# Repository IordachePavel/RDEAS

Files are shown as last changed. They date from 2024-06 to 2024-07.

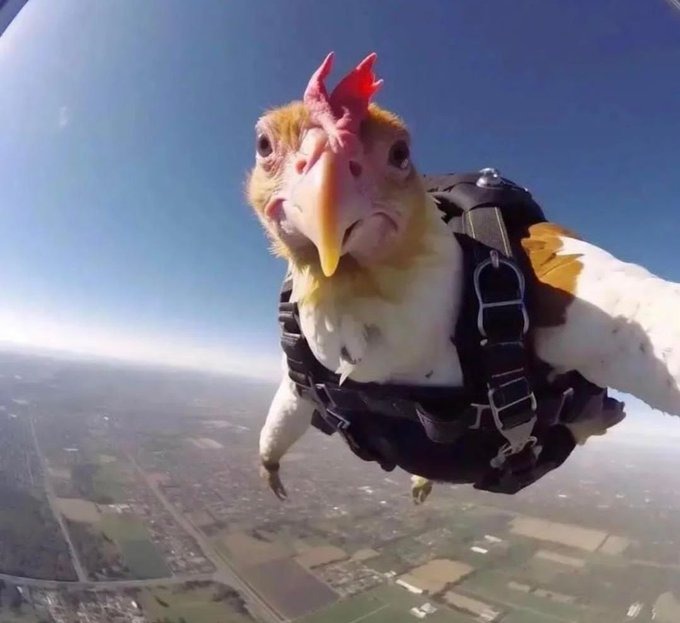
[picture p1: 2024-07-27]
Robot_Controll_doohickey/Resources/skydiving kok [World's funniest image].jpeg

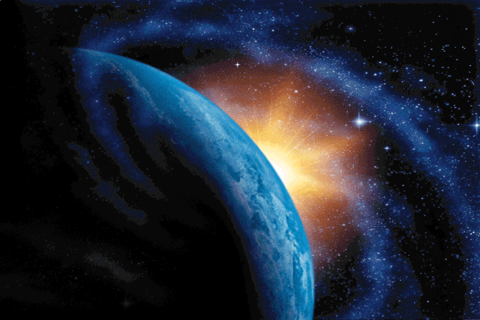
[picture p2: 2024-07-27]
Robot_Controll_doohickey/Resources/background1.bmp

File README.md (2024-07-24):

# Descriere
Remote Dangerous Environment Assessment System (Sistem de Evaluare a Mediilor Periculoase la Distanță)
Sistemul RDEAS este destinat explorării și supravegherii mediilor inaccesibile sau periculoase pentru oameni. Setul RDEAS este compus dintr-un dispozitiv de control la distanță pentru navigație de bază și măsurarea senzorilor, Un set de 2 senzori interschimbabili (Contor Geiger și Senzor de umititate, temperatură și prezența gazelor explozibile), precum și robotul de supraveghere.

# Tehnologii
Sisteme mecanice:
Sistemul este împărțit în 2 părți:

Turela de scanare
Sistem de deplasare

Turela de scanare:


Alcătuită din două motoare , comutatoare de limită și banca de senzori, aceasta se poate roti cu 300° pe orizontală iar banca de senzori cu 270° balans vertical. 

Sistem de deplasare:
Compus din 4 motoare, controlate câte 2 deodată pentru mișcare și viraj tip tanc.

# Sisteme Electronice:
Partea electronică este compusă din:

# Dispozitivul de control
Circuitul de navigare al robotului



Circuitul de interfață pentru senzori

Calculatorul de placă unică „Raspberry Pi 5”


Dispozitivul de control:

Acesta se bazează pe un procesor xscale pocket pc, cu o frecvență de 400MHz, 64 MB de RAM și 64 de ROM, cu o interfață intermediară bazată pe MCU-ul atmel care permite depanarea ușoară și utilizarea unui afișaj de informații secundar. Portul serial DB-9 de pe dispozitiv este conform standardelor RS-232 și poate comunica cu majoritatea dispozitivelor care au o astfel de conexiune. Dispozitivul de control la distanță este echipat cu două baterii, una principală și una secundară. Pentru funcționare, este necesară doar prima. Dispozitivul de control la distanță beneficiază de aproximativ 12 ore de funcționare continuă din prima baterie, iar cea de-a doua baterie este opțională și este utilizată doar pentru a rula pocket pc-ul.

Circuitul de navigare al robotului: Acesta are rolul de control al sistemelor mecanice Pentru calibrarea poziției de 0 a comenzilor de rotire pentru turelă, se folosesc doi senzori magnetici. Banca de senzori este alcătuită dintr-un senzor ultrasonic de distanță, o cameră web și o termopilă digitală IR.

Circuitul de interfață pentru senzori:
Acesta are la bază chipul RP-2040, se ocupă prin interfațarea senzorului interschimbabil și a senzorilor de pe turelă. Acesta preia informațiile de la senzori și îi transmite prin USB la calculatorul de placă unică.
Module de senzori:
Numărător cu tub Geiger-Muller
Senzor temperatură și umiditate ambientală + Senzor concentrație gaz explozibil


Calculatorul de placă unică „Raspberry Pi 5”:
Acesta se ocupă cu procesarea datelor și interpretarea acestora pentru operații autonome, totodată controlând sistemele mecanice și recepționând/transmițând informații de la/la telecomandă prin portul serial, sau prin Ethernet de la/la un calculator.

# Componenta Software:
Componentele software sunt împărțite pe 3 categorii: 1. Program telecomandă 2. Programul microcontroller robot Program telecomandă: Scris in C# pentru platforma Windows Mobile, utilizând sistemele .NET Compact pentru interfața grafică și alte funcții „Low-level”, este folosit pentru interacționarea dintre utilizator și robot. Aceasta are 2 funcții principale.

Terminal serial RS-232
Telecomandă robot Primul mod reprezintă o interfață pentru orice sistem cu o conecțiune serial RS-232, unde utilizatorul poate trimite și recepționa mesaje la/de la dispozitivul conectat, sau pentru depanarea robotului. Al doilea mod reprezintă o telecomandă simplificată a robotului, unde utilizatorul poate controla funcțiile robotului prin intermediul butoanelor de pe ecran.

Programele microcontrolerelor robotului: Aceasta are ca scop traducerea comenziilor de la telecomandă în semnale de acționare a motoarelor, interpretarea și transmiterea semnalelor de la senzori.

Programe pe SBC-ul Raspberry Pi 5 : Acestea se ocupă cu recepționarea comenzilor, interpretarea acestora, codificarea/decodificarea de date pentru transmitere, controlul sistemelor mecanice, interfață electronice senzori și afișaj cameră.

# Cerinte sistem
Operare de bază (Fără cameră, mod teleghidat): 
Doar telecomanda și robotul, cablu serial, Mufă DB-9, distanța maximă variază cu rata de baud.
Operare avansată:
Hardware: Laptop/Computer cu port Ethernet, Cablu Cat5 cu mufă Ethernet.
Software: Windows 7/8/8.1/10/11, Microsoft .NET (Latest)

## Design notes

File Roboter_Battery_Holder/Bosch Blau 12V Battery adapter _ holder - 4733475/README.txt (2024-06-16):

Bosch Blau 12V Battery adapter / holder by Knrd on Thingiverse: https://www.thingiverse.com/thing:4733475

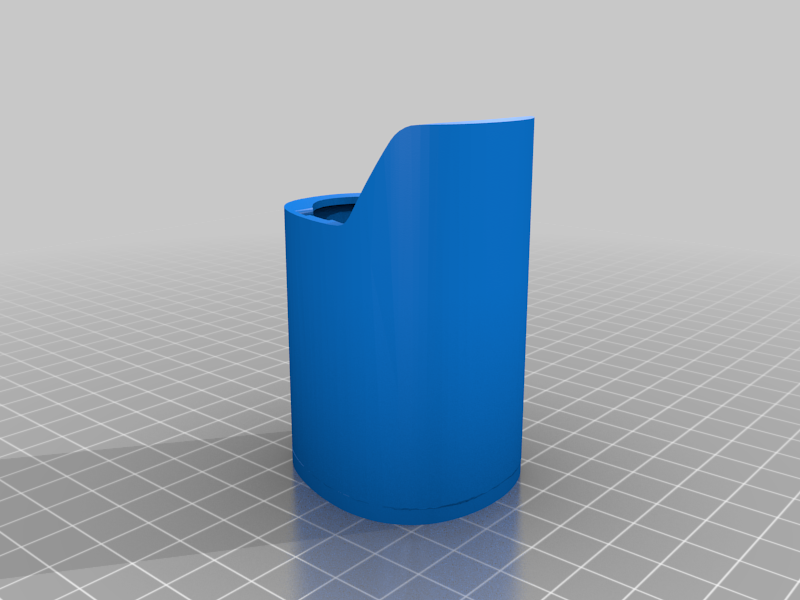
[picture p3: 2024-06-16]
Roboter_Battery_Holder/Bosch Blau 12V Battery adapter _ holder - 4733475/images/Bosch_12V_Battery_Holder.png

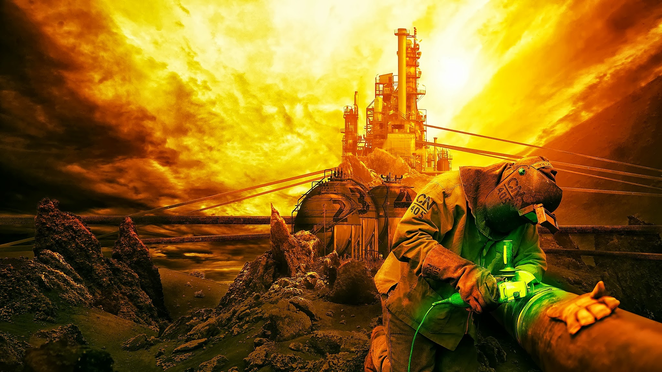
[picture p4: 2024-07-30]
Robot_Controll_doohickey/Resources/factorio man foarte tare.png

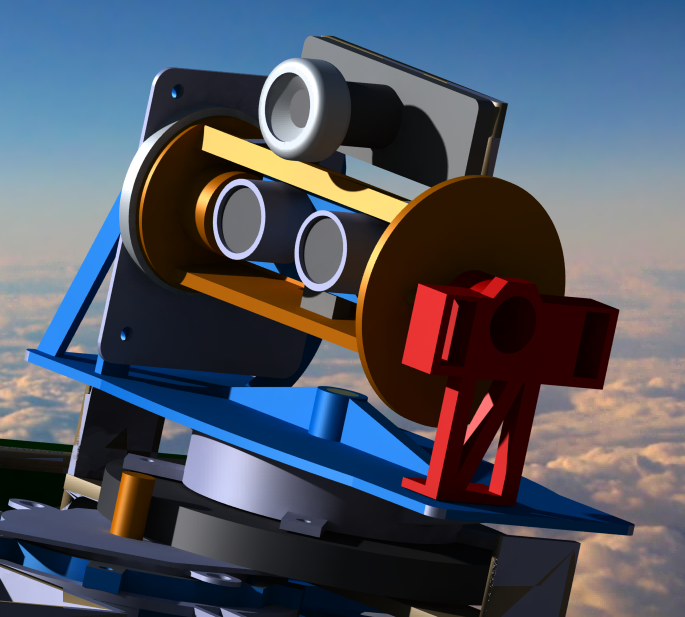
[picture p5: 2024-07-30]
Robot_Controll_doohickey/Resources/SensorTurret.png

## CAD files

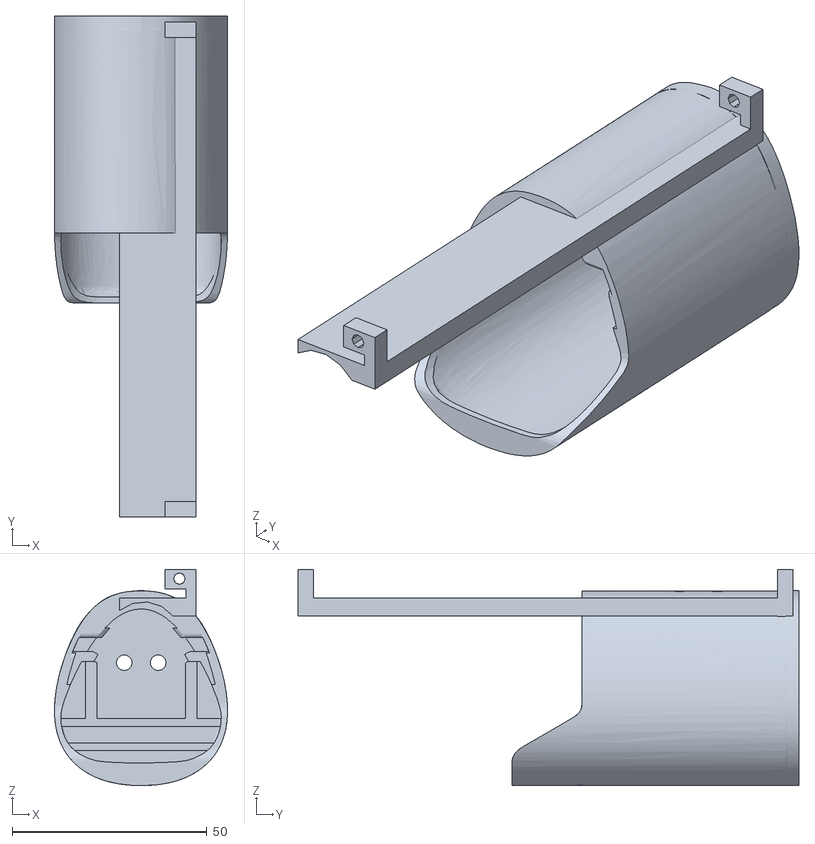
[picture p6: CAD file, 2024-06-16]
Roboter_Battery_Holder/Batery_mount.stl
44.4 x 128.5 x 55.5

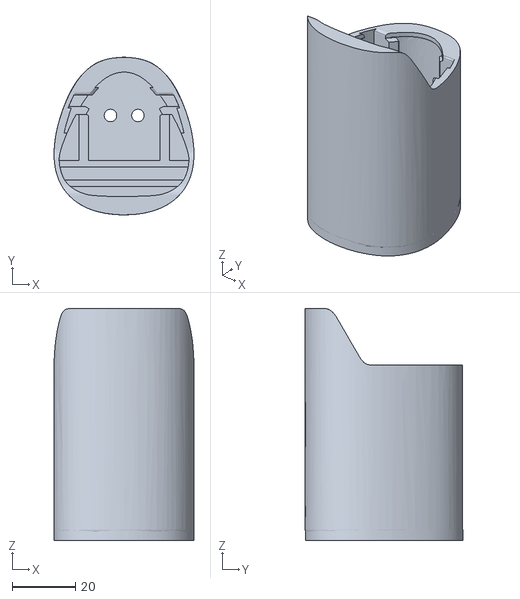
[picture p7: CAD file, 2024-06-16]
Roboter_Battery_Holder/Bosch Blau 12V Battery adapter _ holder - 4733475/files/Bosch_12V_Battery_Holder.stl
44.4 x 50.1 x 73.6

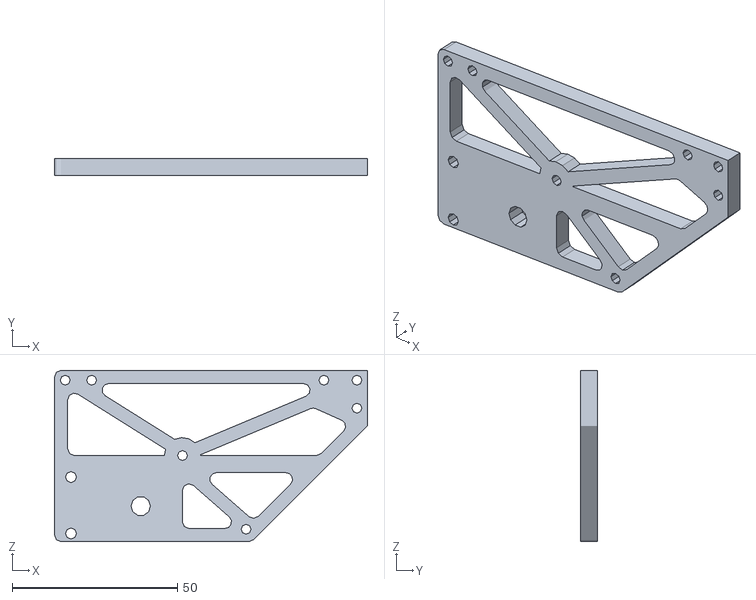
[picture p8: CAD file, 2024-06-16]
Roboter_Chassis/Revision I/Lateral_MotorMount_Frame.stl
94.8 x 5.00 x 51.9

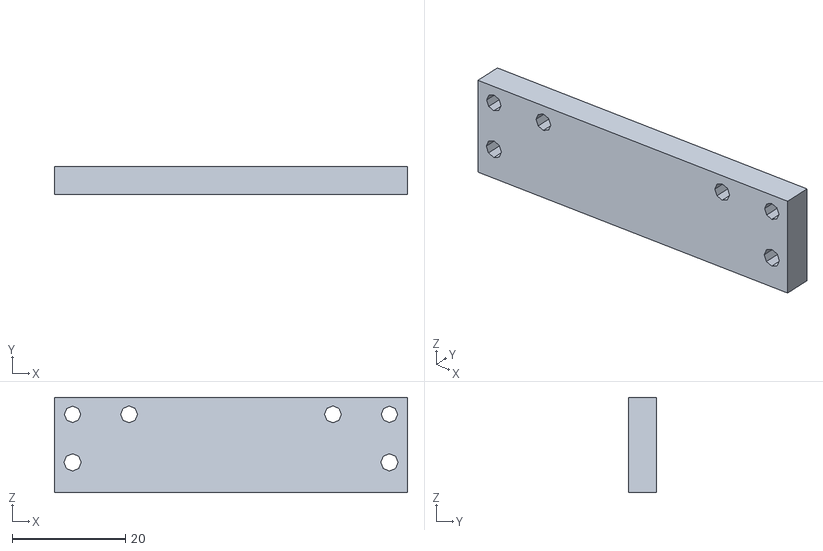
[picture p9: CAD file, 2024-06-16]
Roboter_Chassis/Revision I/Lateral_MotorMount_Frame_JoinArm.stl
62.5 x 5.00 x 16.8

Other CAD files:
AtmosSensorModuleCase/GeigerSensorCase.CATPart
AtmosSensorModuleCase/ModuleSensCap.CATProduct
PDA_REMOTE_CASE/Backside.CATPart
PDA_REMOTE_CASE/Battery Holders.CATPart
PDA_REMOTE_CASE/Casing 1 Rev 2.CATPart
PDA_REMOTE_CASE/Casing 1,.CATPart
PDA_REMOTE_CASE/Casing B.CATPart
PDA_REMOTE_CASE/Casing, 1, side 1.CATPart
PDA_REMOTE_CASE/Casing.CATPart
PDA_REMOTE_CASE/Component_front_panel_1.CATPart
PDA_REMOTE_CASE/Electronics Demo Stand 2.CATPart
PDA_REMOTE_CASE/Electronics Demo Stand.CATPart
PDA_REMOTE_CASE/I don't kow.CATPart
PDA_REMOTE_CASE/IR_THERMOPILE_SENSOR.CATProduct
PDA_REMOTE_CASE/Interface PDA & interpereter display.CATPart
PDA_REMOTE_CASE/Microwave.CATProduct
PDA_REMOTE_CASE/Mini USB B Port.CATPart
PDA_REMOTE_CASE/PDA.CATPart
PDA_REMOTE_CASE/PDA.CATProduct
PDA_REMOTE_CASE/Part1.CATPart
PDA_REMOTE_CASE/Pda-Midframe.CATPart
PDA_REMOTE_CASE/Pushbutton.CATPart
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

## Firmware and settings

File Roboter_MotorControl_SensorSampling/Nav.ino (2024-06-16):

// THIS IS NAVIGATION CIRCUIT CONTROLLER PROGRAM.

//Needed for I2C THERMOPILE SENSOR
#include <Wire.h>

//SENSOR DEFINITIONS
const int trigPin = 16;  //Ultrasonic sensor
const int echoPin = 10; 


#define D6T_ADDR 0x0A  // for I2C 7bit address
#define D6T_CMD 0x4C 

#define PARA_0100MS_1	((uint8_t)0x90)
#define PARA_0100MS_2	((uint8_t)0xDA)
#define PARA_0100MS_3	((uint8_t)0x16)

#define N_ROW 1
#define N_PIXEL 1
#define N_READ ((N_PIXEL + 1) * 2 + 1)

uint8_t rbuf[N_READ];
int16_t pix_data = 0;
int16_t seqData[40] = {0};

float duration, distance; 
uint16_t  totalCount = 0;

//TERMOPILE SENSOR SETTINGS (1)
#define comparingNumInc 16 // x samplingTime ms   (range: 1 to 39)  (example) 16 x 100 ms -> 1.6 sec
#define comparingNumDec 16  // x samplingTime ms  (range: 1 to 39)  (example) 16 x 100 ms -> 1.6 sec
#define threshHoldInc 10 //  /10 degC   (example) 10 -> 1.0 degC (temperature change > 1.0 degC -> Enable)  
#define threshHoldDec 10 //  /10 degC   (example) 10 -> 1.0 degC (temperature change > 1.0 degC -> Disable)

//TERMOPILE SENSOR SETTINGS (2)
#define samplingTime 100

// CONTROL MESSAGE VARIABLE
String MSG;

// SCANNING HEAD CONTROL PINS
const short unsigned int SW_Rot_Lim_1=8;//Rotation Limit Switch Right
const short unsigned int SW_Rot_Lim_2=7;//Rotation Limit Switch Left
const short unsigned int SW_Pit_Lim_1=6;//Pitch Limit Switch Closer
const short unsigned int SW_Pit_Lim_2=9;//Pitch Limit Switch Further
const short unsigned int DriverPitch_Dir=A3;//(Analog pin 3)Pitch motor driver direction
const short unsigned int DriverPitch_Step=A2;//(Analog pin 2)Pitch motor driver step command
const short unsigned int DriverRotation_Dir=4;//Rotation motor driver direction
const short unsigned int DriverRotation_Step=5;//Rotation motor driver step command

const int ButtonCheckCount =100;//How many times to check the switches if they've been triggered during the homing process

// MOVEMENT CONTROL PINS

const short unsigned int T_bridge_Left_Forward = A1;
const short unsigned int T_bridge_Left_Backwards = A0;
const short unsigned int T_bridge_Right_Forward = 15;
const short unsigned int T_bridge_Right_Backwards = 14;   

// MOVEMENT CONTROL VARIABLES
int moveCounter=0;
char dir='F';
// PITCH CONTROL
bool pitchA = false;
bool pitchB = false;
bool yawA = false;
bool yawB = false;


/** <!-- D6T_checkPEC {{{ 1--> D6T PEC(Packet Error Check) calculation.
 * calculate the data sequence,
 * from an I2C Read client address (8bit) to thermal data end.
 */
uint8_t calc_crc(uint8_t data) {
    int index;
    uint8_t temp;
    for (index = 0; index < 8; index++) {
        temp = data;
        data <<= 1;
        if (temp & 0x80) {data ^= 0x07;}
    }
    return data;
}

bool D6T_checkPEC(uint8_t buf[], int n) {
    int i;
    uint8_t crc = calc_crc((D6T_ADDR << 1) | 1);  // I2C Read address (8bit)
    for (i = 0; i < n; i++) {
        crc = calc_crc(buf[i] ^ crc);
    }
    bool ret = crc != buf[n];
    if (ret) {
        Serial.print("PEC check failed:");
        Serial.print(crc, HEX);
        Serial.print("(cal) vs ");
        Serial.print(buf[n], HEX);
        Serial.println("(get)");
    }
    return ret;
}
//PEC END

/** <!-- conv8us_s16_le {{{1 --> convert a 16bit data from the byte stream.
 */
int16_t conv8us_s16_le(uint8_t* buf, int n) {
    int ret;
    ret = buf[n];
    ret += buf[n + 1] << 8;
    return (int16_t)ret;   // and convert negative.
}


// Compare two strings
bool cmpNstr(String a, String b,int n){
  for(int i=0;i<n;i++){
    if(a[i]!=b[i])
    return 0;
  }
  return 1;
}
// Convert message on Serial to task
void MessageInterpreter(char comm){
  int opVal=comm-48;
  if(opVal>0){
    delay(500);
  Serial1.print("RCV");
  Serial.print("Message Awknowledged: ");
  Serial.print(comm);
  }
  switch(opVal){
    case 1:
    Serial1.println("RX OK!");
    break;
    case 2:
    break;
    case 3:
    break;
    case ('F'-48):
    dir='F';
    moveCounter=MSG.substring(5).toInt();
    Serial.println(moveCounter);
    break;
    case ('B'-48):
    dir='B';
    moveCounter=MSG.substring(5).toInt();
    Serial.println(moveCounter);
    break;
    case ('R'-48):
    dir='R';
    moveCounter=MSG.substring(5).toInt();
    Serial.println(moveCounter);
    break;
    case ('L'-48):
    dir='L';
    moveCounter=MSG.substring(5).toInt();
    Serial.println(moveCounter);
    break;
    case ('U'-48):
    digitalWrite(DriverPitch_Dir, 1);
    dir='U'; 
    moveCounter=MSG.substring(5).toInt();
    break;
    case ('D'-48):
    digitalWrite(DriverPitch_Dir, 0);
    dir='D';
    moveCounter=MSG.substring(5).toInt();
    break;
    case ('X'-48):
    digitalWrite(DriverRotation_Dir, 1);
    dir='X';
    moveCounter=MSG.substring(5).toInt();
    break;
    case ('Y'-48):
    digitalWrite(DriverRotation_Dir, 0);
    dir='Y';
    moveCounter=MSG.substring(5).toInt();
    break;
    case ('N'-48):
    moveCounter=1;
    break;
    case ('T'-48):
    TempTarget(0);
    break;
    case('S'-48):
    TempTarget(1);
    break;
    case('P'-48):
    DistTarget();
    break;
  }
  opVal=0;
}

bool HomeYawMotor(){
  yawA = false;
  yawB = false;
  bool SwitchAState = !digitalRead(SW_Rot_Lim_1);
  bool SwitchBState = !digitalRead(SW_Rot_Lim_2);
  if(SwitchAState && SwitchBState){
    return true;
  }
  digitalWrite(DriverRotation_Dir, 1);
  for (int i=0;i<380 && !(yawA && yawB);i++){
    digitalWrite(DriverRotation_Step,HIGH);
    delayMicroseconds(2000);
    digitalWrite(DriverRotation_Step,LOW);
    delayMicroseconds(2000);
    if(SwitchAState != !digitalRead(SW_Rot_Lim_1)){
      yawA = true;
    }
    if(SwitchBState != !digitalRead(SW_Rot_Lim_2)){
      yawB = true;
    }
  }
  digitalWrite(DriverRotation_Dir, 0);
  for (int i=0;i<380*2 && !(yawA && yawB);i++){
    digitalWrite(DriverRotation_Step,HIGH);
    delayMicroseconds(2000);
    digitalWrite(DriverRotation_Step,LOW);
    delayMicroseconds(2000);
    if(SwitchAState != !digitalRead(SW_Rot_Lim_1)){
      yawA = true;
    }
    if(SwitchBState != !digitalRead(SW_Rot_Lim_2)){
      yawB = true;
    }
  }
  if(yawA&&yawB){ // Go just three more steps due to how the magnetic field is aligned to the sensor, it triggers earlier
    for(int i=0;i<3;i++){
    digitalWrite(DriverRotation_Step,HIGH);
    delayMicroseconds(2000);
    digitalWrite(DriverRotation_Step,LOW);
    delayMicroseconds(2000);
    }
  }
    return(yawA&&yawB);
}

bool HomePitchMotor(){
  pitchA = false;
  pitchB = false;
  bool SwitchAState = !digitalRead(SW_Pit_Lim_1);
  bool SwitchBState = !digitalRead(SW_Pit_Lim_2);
  if(SwitchAState && SwitchBState){
    return true;
  }
  digitalWrite(DriverPitch_Dir, 1);
  for (int i=0;i<246 && !(pitchA && pitchB);i++){
    digitalWrite(DriverPitch_Step,HIGH);
    delayMicroseconds(2000);
    digitalWrite(DriverPitch_Step,LOW);
    delayMicroseconds(2000);
    if(SwitchAState != !digitalRead(SW_Pit_Lim_1)){
      pitchA = true;
    }
    if(SwitchBState != !digitalRead(SW_Pit_Lim_2)){
      pitchB = true;
    }
  }
  digitalWrite(DriverPitch_Dir, 0);
  for (int i=0;i<256*2 && !(pitchA && pitchB);i++){
    digitalWrite(DriverPitch_Step,HIGH);
    delayMicroseconds(2000);
    digitalWrite(DriverPitch_Step,LOW);
    delayMicroseconds(2000);
    if(SwitchAState != !digitalRead(SW_Pit_Lim_1)){
      pitchA = true;
    }
    if(SwitchBState != !digitalRead(SW_Pit_Lim_2)){
      pitchB = true;
    }
  }
  if(pitchA&&pitchB){ // Go just three more steps due to how the magnetic field is aligned to the sensor, it triggers
    for(int i=0;i<3;i++){
    digitalWrite(DriverPitch_Step,HIGH);
    delayMicroseconds(2000);
    digitalWrite(DriverPitch_Step,LOW);
    delayMicroseconds(2000);
    }
  }
    return(pitchA&&pitchB);
}

void TempTarget (bool RQST){
    int i, j;

    memset(rbuf, 0, N_READ);
    // Wire buffers are enough to read D6T-16L data (33bytes) with
    // MKR-WiFi1010 and Feather ESP32,
    // these have 256 and 128 buffers in their libraries.
    Wire.beginTransmission(D6T_ADDR);  // I2C client address
    Wire.write(D6T_CMD);               // D6T register
    Wire.endTransmission();            // I2C repeated start for read
    Wire.requestFrom(D6T_ADDR, N_READ);
    i = 0;
    while (Wire.available()) {
        rbuf[i++] = Wire.read();
    }

    if (D6T_checkPEC(rbuf, N_READ - 1)) {
        return;
    }

    // 1st data is PTAT measurement (: Proportional To Absolute Temperature)
    int16_t itemp = conv8us_s16_le(rbuf, 0);
    if(RQST){
    Serial1.print(itemp / 10.0, 1);
    }

    // loop temperature pixels of each thrmopiles measurements
    for (i = 0, j = 2; i < N_PIXEL; i++, j += 2) {
        itemp = conv8us_s16_le(rbuf, j);
        pix_data = itemp;
        if(!RQST){
          Serial1.print("TMP");
          Serial1.print(itemp / 10.0, 1);  // print PTAT & Temperature
            Serial1.print('\n');   // print delimiter
        }
        }
    }

void DistTarget (){
  digitalWrite(trigPin, LOW);
  delayMicroseconds(2);
  digitalWrite(trigPin, HIGH);
  delayMicroseconds(10);
  digitalWrite(trigPin, LOW);

  duration = pulseIn(echoPin, HIGH);
  distance = (duration*.0343)/2;
  distance = round(distance*100);
  Serial1.print("DST");
  Serial1.print((int)distance);
}

void setup() {
  //Pindef ultrasonics
  pinMode(trigPin, OUTPUT);  
	pinMode(echoPin, INPUT); 
  //Serial1 I/O (UART)
  Serial1.begin(9600);
  //Serial I/O (USB, Debug)
  Serial.begin(9600);

  //Sensor Init Config Block START
  uint8_t para[3] = {0};
    para[0] = PARA_0100MS_1;
		para[1] = PARA_0100MS_2;
		para[2] = PARA_0100MS_3;
 
 
    Serial.begin(115200);  // Serial baudrate = 115200bps
    Wire.begin();  // i2c master

    Wire.beginTransmission(D6T_ADDR);  // I2C client address
    Wire.write(0x02);                  // D6T register
    Wire.write(0x00);                  // D6T register
    Wire.write(0x01);                  // D6T register
    Wire.write(0xEE);                  // D6T register
    Wire.endTransmission();            // I2C repeated start for read
    Wire.beginTransmission(D6T_ADDR);  // I2C client address
    Wire.write(0x05);                  // D6T register
    Wire.write(para[0]);                  // D6T register
    Wire.write(para[1]);                  // D6T register
    Wire.write(para[2]);                  // D6T register
    Wire.endTransmission();            // I2C repeated start for read
    Wire.beginTransmission(D6T_ADDR);  // I2C client address
    Wire.write(0x03);                  // D6T register
    Wire.write(0x00);                  // D6T register
    Wire.write(0x03);                  // D6T register
    Wire.write(0x8B);                  // D6T register
    Wire.endTransmission();            // I2C repeated start for read
    Wire.beginTransmission(D6T_ADDR);  // I2C client address
    Wire.write(0x03);                  // D6T register
    Wire.write(0x00);                  // D6T register
    Wire.write(0x07);                  // D6T register
    Wire.write(0x97);                  // D6T register
    Wire.endTransmission();            // I2C repeated start for read
    Wire.beginTransmission(D6T_ADDR);  // I2C client address
    Wire.write(0x02);                  // D6T register
    Wire.write(0x00);                  // D6T register
    Wire.write(0x00);                  // D6T register
    Wire.write(0xE9);                  // D6T register
    Wire.endTransmission();            // I2C repeated start for read	
  //Sensor Init Config Block END
  

  //Limit switches
  pinMode(SW_Rot_Lim_1,INPUT_PULLUP);
  pinMode(SW_Rot_Lim_2,INPUT_PULLUP);
  pinMode(SW_Pit_Lim_1,INPUT_PULLUP);
  pinMode(SW_Pit_Lim_2,INPUT_PULLUP);
  //Head control
  pinMode(DriverPitch_Dir,OUTPUT);
  digitalWrite(DriverPitch_Dir,LOW);
  pinMode(DriverPitch_Step,OUTPUT);
  digitalWrite(DriverPitch_Step,LOW);
  pinMode(DriverRotation_Dir,OUTPUT);
  digitalWrite(DriverRotation_Dir,LOW);
  pinMode(DriverRotation_Step,OUTPUT);
  digitalWrite(DriverRotation_Step,LOW);
  //Movement control
  pinMode(T_bridge_Left_Backwards, OUTPUT);
  digitalWrite(T_bridge_Left_Backwards, LOW);
  pinMode(T_bridge_Left_Forward,OUTPUT);
  digitalWrite(T_bridge_Left_Forward,LOW);
  pinMode(T_bridge_Right_Backwards,OUTPUT);
  digitalWrite(T_bridge_Right_Backwards,LOW);
  pinMode(T_bridge_Right_Forward,OUTPUT);
  digitalWrite(T_bridge_Right_Forward,LOW);

  //Homing
  if(!HomeYawMotor()){
    Serial.println("Motor failure! Check machine.");
    for(;;);//You don't want the machine to tangle its wires.
  }
  else{
    Serial.println("Yaw motor homing OK!");
  }
  if(!HomePitchMotor()){
    Serial.println("Motor failure! Check machine.");
    for(;;);//Same here.
  }
  else{
    Serial.println("Pitch motor homing OK!");
  }
  delay(100);
  Serial.println("Motor homing success!");
}

void loop() {
  if(Serial1.available() > 0){
  MSG=Serial1.readString();
  if (cmpNstr(MSG,"NAV",3))
  
  MessageInterpreter(MSG[4]);
  }
  //Movement logic (must be in loop so the MCU can switch between driving the motors, running the counter for the motors and using navigation sensors)
  if(moveCounter){
    switch (dir) {
    case 'F':
    digitalWrite(T_bridge_Left_Backwards,LOW);
    digitalWrite(T_bridge_Right_Backwards,LOW);
    digitalWrite(T_bridge_Left_Forward,HIGH);
    digitalWrite(T_bridge_Right_Forward,HIGH);
    break;
    case 'B':
    digitalWrite(T_bridge_Left_Forward,LOW);
    digitalWrite(T_bridge_Right_Forward,LOW);
    digitalWrite(T_bridge_Left_Backwards,HIGH);
    digitalWrite(T_bridge_Right_Backwards,HIGH);
    break;
    case 'R':
    digitalWrite(T_bridge_Left_Forward,HIGH);
    digitalWrite(T_bridge_Right_Forward,LOW);
    digitalWrite(T_bridge_Left_Backwards,LOW);
    digitalWrite(T_bridge_Right_Backwards,HIGH);
    break;
    case 'L':
    digitalWrite(T_bridge_Left_Forward,LOW);
    digitalWrite(T_bridge_Right_Forward,HIGH);
    digitalWrite(T_bridge_Left_Backwards,HIGH);
    digitalWrite(T_bridge_Right_Backwards,LOW);
    break;
    case 'U':
    digitalWrite(DriverPitch_Step,HIGH);
    delayMicroseconds(2000);
    digitalWrite(DriverPitch_Step,LOW);
    delayMicroseconds(2000);
    break;
    case 'D':
    digitalWrite(DriverPitch_Step,HIGH);
    delayMicroseconds(2000);
    digitalWrite(DriverPitch_Step,LOW);
    delayMicroseconds(2000);
    break;
    case 'X':
    digitalWrite(DriverRotation_Step,HIGH);
    delayMicroseconds(2000);
    digitalWrite(DriverRotation_Step,LOW);
    delayMicroseconds(2000);
    break;
    case 'Y':
    digitalWrite(DriverRotation_Step,HIGH);
    delayMicroseconds(2000);
    digitalWrite(DriverRotation_Step,LOW);
    delayMicroseconds(2000);
    break;
    }
    moveCounter--;
    Serial.println(moveCounter);
    Serial.print(dir);
    if(moveCounter == 1){
      DistTarget();
    }
  }
  else{
    digitalWrite(T_bridge_Left_Backwards,LOW);
    digitalWrite(T_bridge_Left_Forward,LOW);
    digitalWrite(T_bridge_Right_Backwards,LOW);
    digitalWrite(T_bridge_Right_Forward,LOW);
  }

}

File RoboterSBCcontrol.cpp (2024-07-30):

#include <iostream>
#include <unistd.h>
#include <sys/socket.h>
#include <netinet/in.h>
#include <string>
#include <cstring>
#include <wiringPi.h>
#include <libserialport.h>
#include <thread>
#include <sstream>

#define Right_T_bridge_Forwards 12
#define Right_T_bridge_Backwards 13
#define Left_T_bridge_Forwards 14
#define Left_T_bridge_Backwards 21
#define Rot_Stp 2
#define Rot_Dir 3
#define Pit_Stp 22
#define Pit_Dir 23
#define Sw_Rot_Lim_1 7
#define Sw_Rot_Lim_2 9
#define Sw_Pit_Lim_1 8
#define Sw_Pit_Lim_2 0

char PinMotorCommand = 'S';
bool StepperCommandEnable = false;
bool AlreadyStopped = true;
bool AlreadyStoppedRotation = true;

sp_port *port1;
sp_port *port2;
sp_port *raspberryPiUartPort; // New serial port for Raspberry Pi UART

// Function prototypes
void configure_port(sp_port *port);
void initialize_serial_ports();
void close_serial_ports();
void SendUSBUART1(const std::string &message);
void SendUSBUART2(const std::string &message);
std::string ReceiveUSBUART(sp_port *port);
void handleRotCommand(char movCommand);
void StepperMovementHandler(char movCommand);
void handleMovCommand(char movCommand);
void handleSNSCommand(char command);
void interpretMessage(const std::string& message);
void forwardMessageToClient(const std::string &message, int client_socket);
void handleRaspberryPiUartCommunication();

void configure_port(sp_port *port) {
    sp_set_baudrate(port, 9600);
    sp_set_bits(port, 8);
    sp_set_parity(port, SP_PARITY_NONE);
    sp_set_stopbits(port, 1);
    sp_set_flowcontrol(port, SP_FLOWCONTROL_NONE);
}

void initialize_serial_ports() {
    if (sp_get_port_by_name("/dev/ttyACM1", &port2) != SP_OK) {
        std::cerr << "Failed to get port /dev/ttyACM1" << std::endl;
        exit(1);
    }
    if (sp_open(port2, SP_MODE_READ_WRITE) != SP_OK) {
        std::cerr << "Failed to open port /dev/ttyACM1" << std::endl;
        exit(1);
    }
    configure_port(port2);

    if (sp_get_port_by_name("/dev/ttyACM0", &port1) != SP_OK) {
        std::cerr << "Failed to get port /dev/ttyACM0" << std::endl;
        sp_close(port1);
        exit(1);
    }
    if (sp_open(port1, SP_MODE_READ_WRITE) != SP_OK) {
        std::cerr << "Failed to open port /dev/ttyACM0" << std::endl;
        sp_close(port1);
        exit(1);
    }
    configure_port(port1);

    // Open Raspberry Pi UART port
    if (sp_get_port_by_name("/dev/ttyAMA0", &raspberryPiUartPort) != SP_OK) {
        std::cerr << "Failed to get port /dev/ttyAMA0" << std::endl;
        sp_close(port1);
        sp_close(port2);
        exit(1);
    }
    if (sp_open(raspberryPiUartPort, SP_MODE_READ_WRITE) != SP_OK) {
        std::cerr << "Failed to open port /dev/ttyAMA0" << std::endl;
        sp_close(port1);
        sp_close(port2);
        exit(1);
    }
    configure_port(raspberryPiUartPort);
}

void close_serial_ports() {
    sp_close(port1);
    sp_close(port2);
    sp_close(raspberryPiUartPort);
    sp_free_port(port1);
    sp_free_port(port2);
    sp_free_port(raspberryPiUartPort);
}

void SendUSBUART1(const std::string &message) {
    sp_nonblocking_write(port1, message.c_str(), message.length());
}

void SendUSBUART2(const std::string &message) {
    sp_nonblocking_write(port2, message.c_str(), message.length());
}

std::string ReceiveUSBUART(sp_port *port) {
    char buffer[1024];
    int bytes_read = sp_blocking_read(port, buffer, sizeof(buffer) - 1, 1000); // Timeout of 1000 ms
    if (bytes_read > 0) {
        buffer[bytes_read] = '\0';
        return std::string(buffer);
    }
    return "";
}

void handleRotCommand(char movCommand) {
    StepperCommandEnable = true;
    PinMotorCommand = movCommand;
    std::cout << "Handling ROT command: " << movCommand << std::endl;
}

bool HomeYawMotor(){
    std::cout << "Homing yaw" << std::endl;
  bool yawA = false;
  bool yawB = false;
  bool SwitchAState = !digitalRead(Sw_Rot_Lim_1);
  bool SwitchBState = !digitalRead(Sw_Rot_Lim_2);
  if(SwitchAState && SwitchBState){
    return true;
  }
  digitalWrite(Rot_Dir, 1);
  for (int i=0;i<380 && !(yawA && yawB);i++){
    digitalWrite(Rot_Stp,HIGH);
    delay(5);
    digitalWrite(Rot_Stp,LOW);
    delay(5);
    if(SwitchAState != !digitalRead(Sw_Rot_Lim_1)){
      yawA = true;
    }
    if(SwitchBState != !digitalRead(Sw_Rot_Lim_2)){
      yawB = true;
    }
  }
  digitalWrite(Rot_Dir, 0);
  for (int i=0;i<380*2 && !(yawA && yawB);i++){
    digitalWrite(Rot_Stp,HIGH);
    delay(5);
    digitalWrite(Rot_Stp,LOW);
    delay(5);
    if(SwitchAState != !digitalRead(Sw_Rot_Lim_1)){
      yawA = true;
    }
    if(SwitchBState != !digitalRead(Sw_Rot_Lim_2)){
      yawB = true;
    }
  }
  if(yawA&&yawB){ // Go just three more steps due to how the magnetic field is aligned to the sensor, it triggers earlier
    for(int i=0;i<3;i++){
    digitalWrite(Rot_Stp,HIGH);
    delay(5);
    digitalWrite(Rot_Stp,LOW);
    delay(5);
    }
  }
    return(yawA&&yawB);
}

bool HomePitchMotor(){
  bool pitchA = false;
  bool pitchB = false;
  bool SwitchAState = !digitalRead(Sw_Pit_Lim_1);
  bool SwitchBState = !digitalRead(Sw_Pit_Lim_2);
  if(SwitchAState && SwitchBState){
    return true;
  }
  digitalWrite(Pit_Stp, 1);
  for (int i=0;i<246 && !(pitchA && pitchB);i++){
    digitalWrite(Pit_Stp,HIGH);
    delay(2);
    digitalWrite(Pit_Stp,LOW);
    delay(2);
    if(SwitchAState != !digitalRead(Sw_Pit_Lim_1)){
      pitchA = true;
    }
    if(SwitchBState != !digitalRead(Sw_Pit_Lim_2)){
      pitchB = true;
    }
  }
  digitalWrite(Pit_Dir , 0);
  for (int i=0;i<256*2 && !(pitchA && pitchB);i++){
    digitalWrite(Pit_Stp,HIGH);
    delay(2);
    digitalWrite(Pit_Stp,LOW);
    delay(2);
    if(SwitchAState != !digitalRead(Sw_Pit_Lim_1)){
      pitchA = true;
    }
    if(SwitchBState != !digitalRead(Sw_Pit_Lim_2)){
      pitchB = true;
    }
  }
  if(pitchA&&pitchB){ // Go just three more steps due to how the magnetic field is aligned to the sensor, it triggers
    for(int i=0;i<3;i++){
    digitalWrite(Pit_Stp,HIGH);
    delay(2);
    digitalWrite(Pit_Stp,LOW);
    delay(2);
    }
  }
    return(pitchA&&pitchB);
}

void StepperMovementHandler(char movCommand) {
    if (movCommand == 'B') {
        digitalWrite(Rot_Dir, HIGH);
        digitalWrite(Rot_Stp, HIGH);
        delay(2);
        digitalWrite(Rot_Stp, LOW);
        digitalWrite(Rot_Dir, LOW);
    } else if (movCommand == 'D') {
        digitalWrite(Pit_Dir, HIGH);
        digitalWrite(Pit_Stp, HIGH);
        delay(2);
        digitalWrite(Pit_Stp, LOW);
        digitalWrite(Pit_Dir, LOW);
    } else if (movCommand == 'A') {
        digitalWrite(Rot_Stp, HIGH);
        delay(2);
        digitalWrite(Rot_Stp, LOW);
    } else if (movCommand == 'C') {
        digitalWrite(Pit_Stp, HIGH);
        delay(2);
        digitalWrite(Pit_Stp, LOW);
    }
}
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

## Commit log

2024-06-18 Rename HEY LOIS IM MIDFRAME.CATPart to Pda-Midframe.CATPart
    [Pda-Midframe.CATPart]
2024-07-02 Update PDA_MCU_INTERFACE.ino
    The gaming update (Support for joysticks in order to send control via serial, added ability for the PDA to change the baud rate at will, which originally was stuck to 9600 baud.)
    [PDA_MCU_INTERFACE.ino]
2024-07-02 Update PDA_MCU_INTERFACE.ino
    Whoopsies, small display order error, junk text from last message would remain, added clean function where possible.
    [PDA_MCU_INTERFACE.ino]
2024-07-24 Create Sensor_Module_Reader.ino
    Logic for the modular sensor reader
2024-07-24 Create Sensor_AmbientTemperatureHumidity_EGM.ino
    Logic for the ambient temperature, humidity, and explosive gas concentration in the atmosphere sensor.
2024-07-27 Modular sensor cases
    [GeigerSensorCase.CATPart, ModuleSensCap.CATProduct]
2024-07-27 New desktop robot control program 1.0
    New desktop control program that allows the user to control the robot via LAN connection, enabling sensor measurement requests and movement control. This version has PDA remote control in serial joys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
2024-07-27 Create Turret_Sensor_5V_Controller.ino
    Additional MCU to handle talking to the 5V sensor. I ain't taking care of stepping down the 5V back to 3.3 volts for the microcomputer, so it might as well be USB. Plus be it serial or be it USB, its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
2024-07-30 Create CameraProgram.py
    Program for streaming camera feed
2024-07-30 Update CameraProgram.py
    Camera Program
2024-07-30 Update RoboterSBCcontrol.cpp
    Minor improvements, homing YAW on the turret is now possible.
